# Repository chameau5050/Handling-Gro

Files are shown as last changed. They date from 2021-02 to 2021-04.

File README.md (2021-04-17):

<div id="Handling GRO!">
    <h1>Handling GRO</h1>
    <h3>Projet S4 Université de Sherbrooke</h3>
    <h3>UdeS-GRO | 65<sup>th</sup> Promotion | 2021</h3>
</div>

[//]: # (------------------------------------------------)

<div id="badges">

 

</div>

[//]: # (------------------------------------------------)

**This is an academic project by robotics engineering students at Université de Sherbrooke.**
**Handling GRO is a four degrees of freedom robot.**

<div id="platform" align="center">
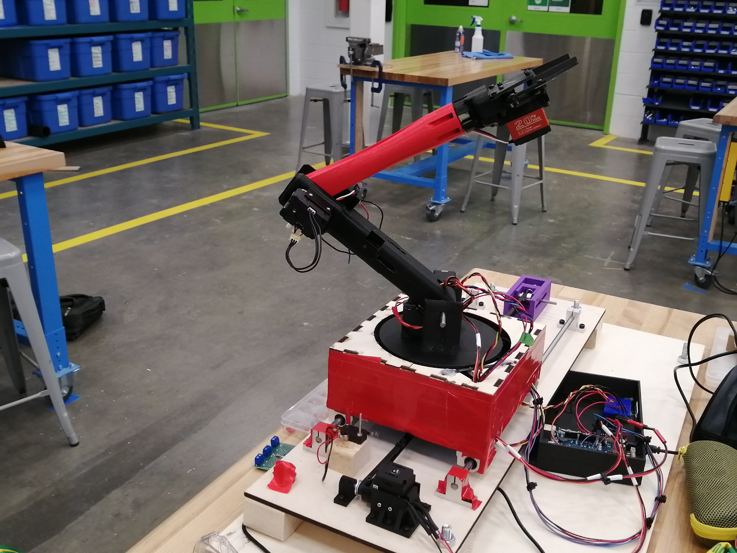
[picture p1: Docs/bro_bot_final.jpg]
Robot Assembly
    
</div>

## Table of Contents
- [Authors](#Authors)
- [Setup](#Setup)
- [Documentation](#Documentation)
- [Recommended manufacturing device](#Recommended_device)
- [External Resources](#Resources)
    - [Single-Board Computer](#Computer)
    - [Controller_OpenCr](#Controller)
    - [Dynamixel motors](#dynamixel) 
    - [Steppermotor](#StepperMotor)
    - [DriveBoard (with steppermotor)](#DriveBoard)
    - [Servomotor](#ServoMotor)
    - [Power Supply: Motor/(OpenCr or Arduino)](#Power)
    - [Linear Rods](#Rods)
    - [Linear bearing](#linear_bearing)
    - [Timing belt](#Timing_belt)
- [License](#License)

[//]: # (------------------------------------------------)
## Authors
- Olivier Demers - _Initial work_ - [chameau5050](https://github.com/chameau5050)
- Jérémy Giguère - _Initial work_ - [gigj1302](https://github.com/gigj1302)
- Philippe Gadeyne - _Initial work_ - [gadp1401](https://github.com/gigj1302)
- Francis Amyot - _Initial work_ - [FrancisAmyot](https://github.com/FrancisAmyot)
- Vincent-Xavier Voyer - _Initial work_ - [Theparky105](https://github.com/Theparky105)

## Setup

1. Buy the component in the [External Resources](#Resources) section.
2. Use the [CAD models](https://github.com/chameau5050/Handling-Gro/tree/main/Mechanical/STL%20(For%203D%20printing)) to 3D print all the different parts of the robot.
3. Assemble the robot according to the [assembly guide](https://github.com/chameau5050/Handling-Gro/blob/main/Docs/Doc_mecanical/Assembly%20manual.pdf).
4. Do the electrical connections using the [electrical schematics](https://github.com/chameau5050/Handling-Gro/blob/main/Electrical_hardware/electrical_wiring_V1.pdf) in the documentation section.
4. Set up the [Raspberry Pi](#Computer) by connecting it with the [OpenCr](#Controller_OpenCr), your computer and the to a power source.
5. Download or clone the repository in the Raspberry Pi.
6. Verify your Python version (3.5 and above) and the port series.
7. Build and transfer all the code to the OpenCr (or Arduino). See [Compilation procedure](https://github.com/chameau5050/Handling-Gro/wiki/setup-IDE-for-ControlMotor(OpenCr)) documentation.
8. Build and transfer all the code to Raspberry Pi. See [Compilation procedure](https://github.com/chameau5050/Handling-Gro/wiki/setup-IDE-for-Application) documentation.
8. Open the interface and look your new Handgling GRO robot in action.
8. Congigure UI with Qt
9. For more information, see the [documentation](https://github.com/chameau5050/Handling-Gro/wiki) section
## Documentation

All the different information is available [here](https://github.com/chameau5050/Handling-Gro/wiki) in the project wiki.

## Recommended manufacturing device
The following rapid design devices are required for this project are:
- For plastic part 
  - 3D Printer
  
- For wood part (choose one of the 2 following choices) 
  - Laser cutter
  - Basic tools for wood (drill, saw, sand paper, ...)

## External Resources
This section specifies the external resources used in the project.

#### Single-Board Computer
- Brand: [Raspberry Pi](https://www.raspberrypi.org/products/raspberry-pi-3-model-b-plus/)
- Model: Raspberry Pi 3 Model 3B+
- Quantity: 1

#### Microcontroller
- Brand: [OpenCr](https://store.arduino.cc/mega-2560-r3)
- Model: OpenCr
- Quantity: 1

#### Microcontroller (optional)
- Brand: [Arduino](https://store.arduino.cc/mega-2560-r3)
- Model: Mega 2560 REV3
- Quantity: 1
- **If you want to use other motors than dynamixel motors, you can.

#### Dynamixel_motors
- Brand: [Dynamixel](https://www.robotis.us/dynamixel-xm430-w350-r/)
- Model: XM430-W350
- Quantity: 4

#### Steppermotor
- Brand: [Elegoo](https://www.elegoo.com/products/elegoo-uln2003-5v-stepper-motor-uln2003-driver-board)
- Model: 28BYJ-48 
- Quantity: 1

#### DriveBoard (with steppermotor)
- Brand: [Elegoo](https://www.elegoo.com/products/elegoo-uln2003-5v-stepper-motor-uln2003-driver-board)
- Model: ULN2003 
- Quantity: 1

#### Servomotor
- Brand: [Miuzei](https://www.amazon.ca/-/fr/Miuzei-num%C3%A9rique-%C3%A9tanche-voiture-contr%C3%B4le/dp/B07MDM1C3M)
- Model: Miuzei Servo Motor 20 Kg
- Quantity: 1

#### Power Supply: Motor/(OpenCr or Arduino)
- Brand: [PowerPayless Inc](https://www.amazon.com/7-5A-Power-Adapter-Device-Payless/dp/B01CYZWAWY)
- Model: B01CYZWAWY (65107)
- Quantity: 1

####  Linear Rods
- Brand: [yqltd](https://www.amazon.ca/CNBTR-Horizontal-Bearing-Bushing-Optical/dp/B01KLE9QEU)
- ASIN: CNBTR4040 road
- Quantity: 2

####  Linear bearing
- Brand: [yqltd](https://www.amazon.ca/CNBTR-Horizontal-Bearing-Bushing-Optical/dp/B01KLE9QEU)
- ASIN: CNBTR4040 bearing
- Quantity: 4

####  Timing belt
- Brand: [Uranny](https://www.amazon.ca/gp/product/B071HKC52V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)
- ASIN: Timing Belt 6mm Wide & 10X 5MM Pulley for 3D Printer
- Quantity: 1

## License
This project is licenced under a   license.

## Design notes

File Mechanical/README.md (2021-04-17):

# Mechanical

All the parts that need to be 3D printed are in the STL folder, see the BOM in the [wiki](https://github.com/chameau5050/Handling-Gro/wiki) to know the number required and to see the step by step assembly guide.

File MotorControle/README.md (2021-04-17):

# Handling-Gro MotorControle section

This is where we implement all the motor control part

Choose if you want to use OpenCr bord or an other board for the motor control.

click on this [link](https://github.com/chameau5050/Handling-Gro/wiki/Motor-Control:-Choice-of-microcontroller) to help you make your choice

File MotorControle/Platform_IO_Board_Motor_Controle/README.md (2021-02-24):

# Handling-Gro

here we implement the All the motor controle part

curently code is running on arduino Mega and can be edit with Visual Studio code with Platform IO extension.

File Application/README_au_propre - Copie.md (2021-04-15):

<div id="Handling GRO">
    <h1>Handling GRO</h1>
    <h3>Projet S4 Université de Sherbrooke</h3>
    <h3>UdeS-GRO | 65<sup>th</sup> Promotion | 2021</h3>
</div>

[//]: # (------------------------------------------------)

<div id="badges">

 

</div>

[//]: # (------------------------------------------------)

**Decrire notre projet en quelques lignes
This is an academic project by robotics engineering undergraduates at Université de Sherbrooke.**
**Handling GRO is a five degrees of freedom fanuc robot. This is an academic project by robotics engineering undergraduates at l'Université de Sherbrooke.**

<div id="platform" align="center">
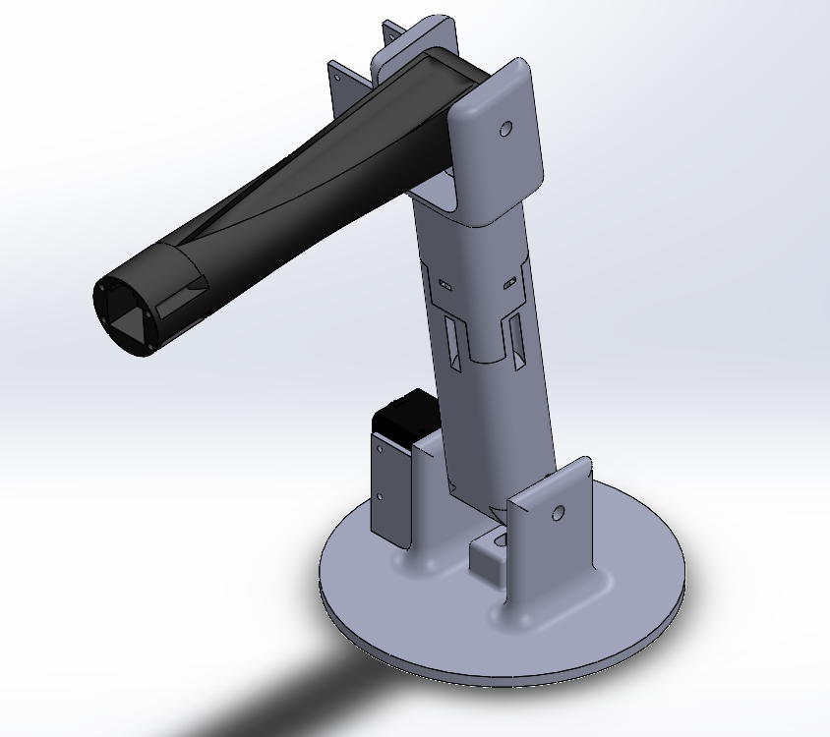
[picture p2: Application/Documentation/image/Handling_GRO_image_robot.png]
Robot Assembly
    
</div>

## Table of Contents
- [Setup](#Setup)
- [Documentation](#Documentation)
- [Platform Operation](#Operation)
- [External Resources](#Resources)
    - [Single-Board Computer](#Computer)
    - [Microcontroller](#Controller)
    - [Servomotors](#Servo)
    - [Power Supply: Motor/Arduino](#Power)
    - [Servo Rods](#Rods)

[//]: # (------------------------------------------------)

## Setup
1. Buy the component in the [External Resources](#Resources) section.
2. Use the [CAD models](https://github.com/SPUdeS/SPUdeS/tree/main/CADs) to 3D print the [base](https://github.com/SPUdeS/SPUdeS/blob/main/CADs/Base.SLDPRT), the [platform](https://github.com/SPUdeS/SPUdeS/blob/main/CADs/Platform.SLDPRT) and the [servo arms](https://github.com/SPUdeS/SPUdeS/blob/main/CADs/Legs.SLDASM).
3. Do the electrical connections using the [electrical schematics](https://github.com/SPUdeS/SPUdeS/blob/main/Documentation/Electical%20schematics.pdf) in the documentation section.
3. Set up the [Raspberry Pi](#Computer) by connecting it with the [Arduino](#Controller), your computer and the to a power source.
4. Download or clone the repository in the Raspberry Pi.
5. Verify your Python version (3.5 and above) and the port series.
6. Build and transfer all the code to the Arduino and Raspberry Pi.
7. Open the interface and look at the [platform operation](#Operation) section.
## Documentation

The dynamic system can be found in the [Geometric model](https://github.com/SPUdeS/SPUdeS/tree/main/Geometric%20model) folder.
## Platform Operation

The camera feed can show the Stewart platform instantly. The platform can be controlled using the following buttons on the interface:

<div id="Interface">
    Platform Assembly
</div>

- It is possible to enter the angle value of all the motor (by default, all the motor should have the same angle).

- The Homing Button brings the stewart platform at its initial centered position.  

- The Move Up Button brings the stewart platform a bit over its actual position
## External Resources
This section specifies the external resources used in the project.

#### Single-Board Computer
- Brand: [Raspberry Pi](https://www.raspberrypi.org/products/raspberry-pi-3-model-b-plus/)
- Model: Raspberry Pi 3 Model 3B+
- Quantity: 1

#### Microcontroller
- Brand: [Arduino](https://store.arduino.cc/mega-2560-r3)
- Model: Mega 2560 REV3
- Quantity: 1

<!--#### Servomotors
- Brand: [Hitec RCD](https://hitecrcd.com/products/servos/sport-servos/analog-sport-servos/hs-422/product)
- Model: HS-422
- Quantity: 6
-->
#### Dynamixel_motors
- Brand: [Dynamixel](https://www.robotis.us/dynamixel-xm430-w350-r/)
- Model: XM430-W350
- Quantity: 4

#### SteperMotors
- Brand: [Elegoo](https://www.elegoo.com/products/elegoo-uln2003-5v-stepper-motor-uln2003-driver-board)
- Model: 28BYJ-48 
- Quantity: 1

#### DriveBoard
- Brand: [Elegoo](https://www.elegoo.com/products/elegoo-uln2003-5v-stepper-motor-uln2003-driver-board)
- Model: ULN2003 
- Quantity: 1
<!--
#### Servomotors
- Brand: [Adafruit](https://www.amazon.ca/Adafruit-2201-Sub-micro-Servo-SG51R/dp/B0137LG0KW)
- Model: SG51R
- Quantity: 6

#### Power Supply: Motor/Arduino
- Brand: [CUI Inc.](https://www.digikey.com/en/products/detail/cui-inc/SWI10-5-N-P5/6618696)
- Model: SWI10-5-N
- Quantity: 1
-->
####  Linear Rods
- Brand: [yqltd](https://www.amazon.ca/CNBTR-Horizontal-Bearing-Bushing-Optical/dp/B01KLE9QEU)
- ASIN: CNBTR4040 road
- Quantity: 2

####  Linear bearing
- Brand: [yqltd](https://www.amazon.ca/CNBTR-Horizontal-Bearing-Bushing-Optical/dp/B01KLE9QEU)
- ASIN: CNBTR4040 bearing
- Quantity: 4

## License
This project is licenced under a   license.

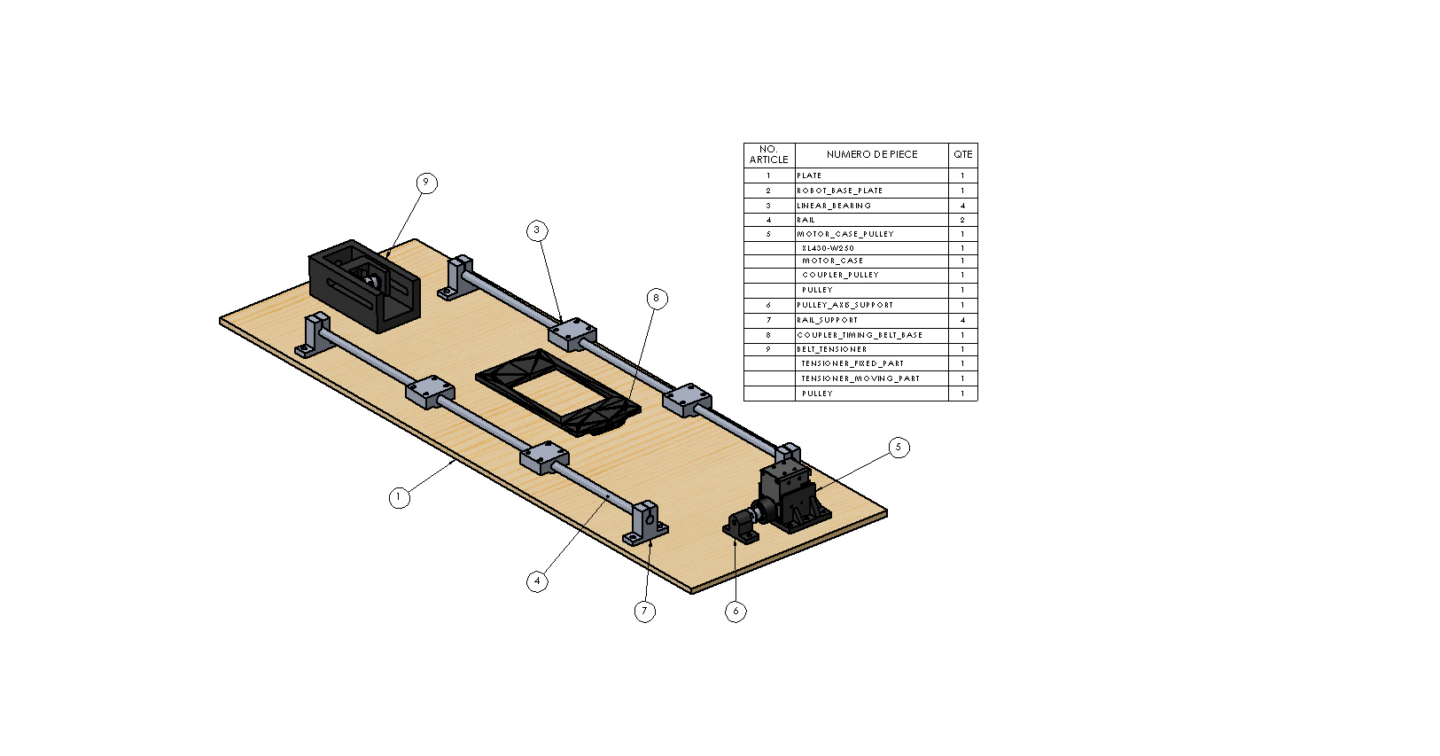
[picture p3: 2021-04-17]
Mechanical/linear_axis/linear_axis_plan.JPG

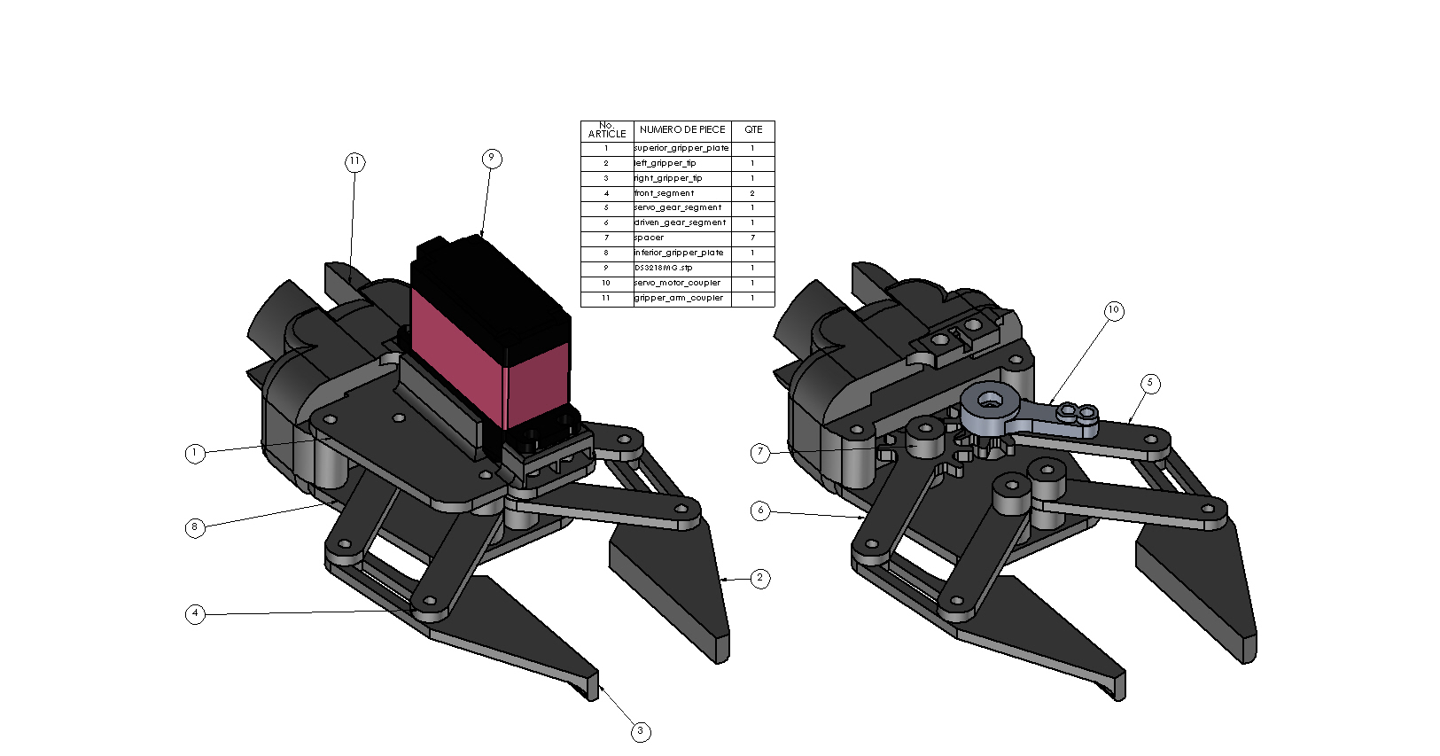
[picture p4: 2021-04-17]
Mechanical/Gripper_servo_motor/gripper_plan.JPG

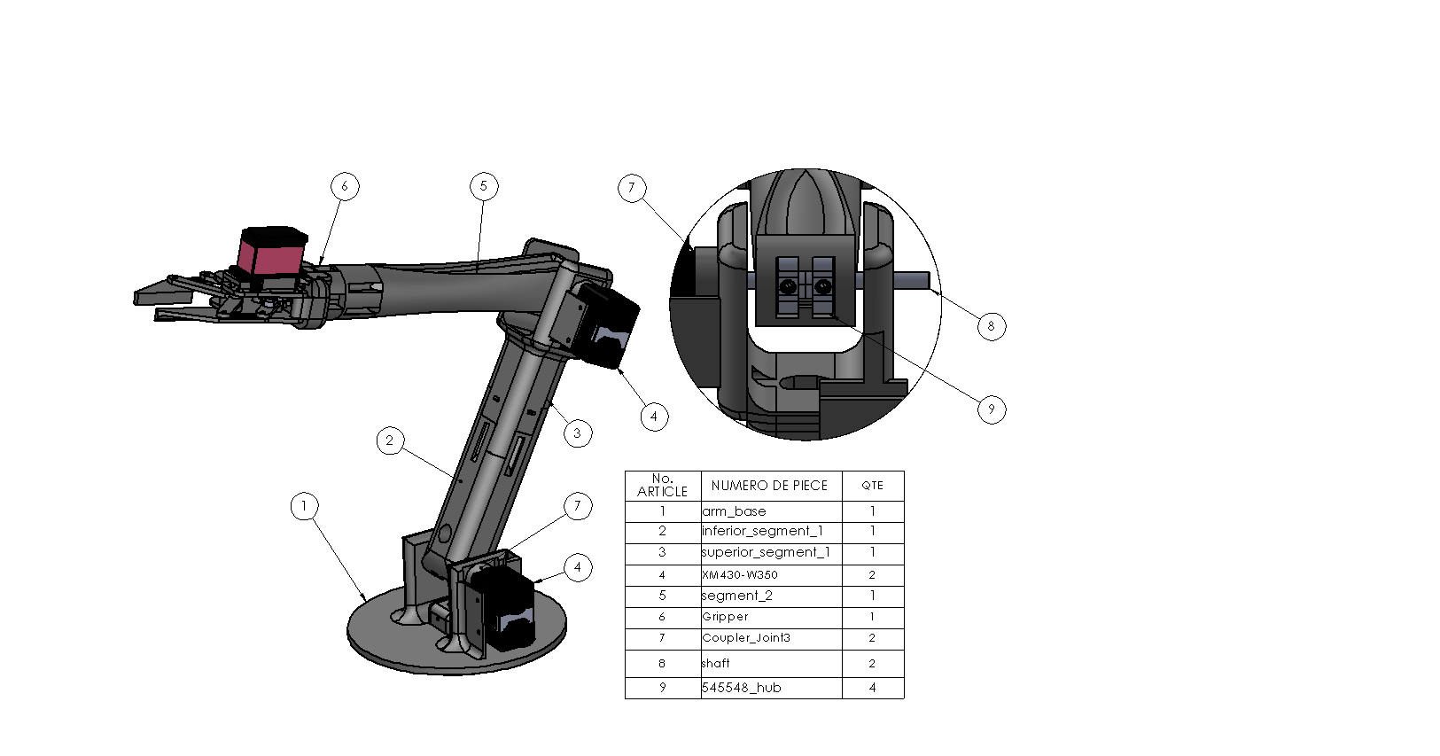
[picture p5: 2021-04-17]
Mechanical/Arm2.0/arm_plan.JPG

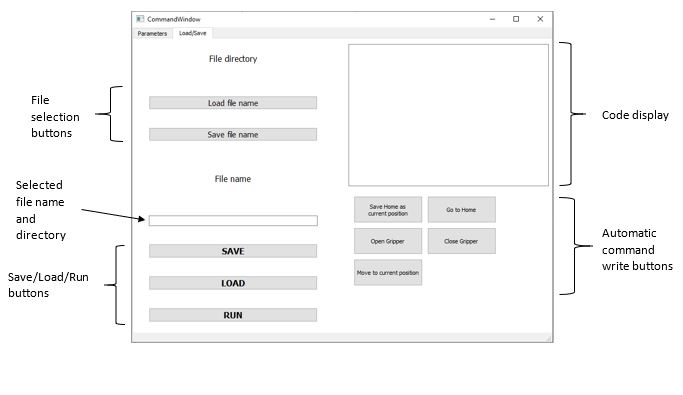
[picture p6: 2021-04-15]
Docs/Doc_picture_UI/Picture_UI_P2.JPG

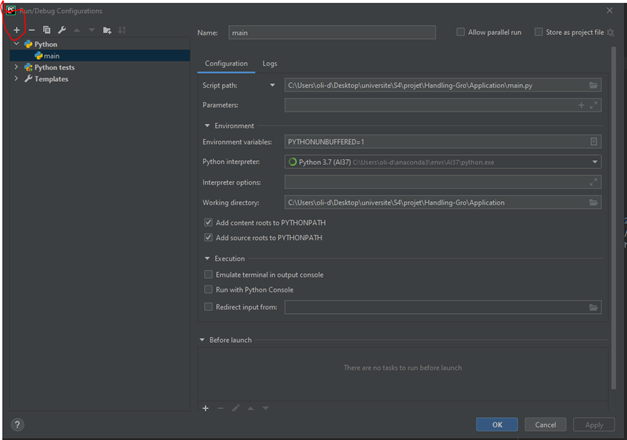
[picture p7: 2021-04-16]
Docs/Doc_picture_Application/addExecutionConfig.png

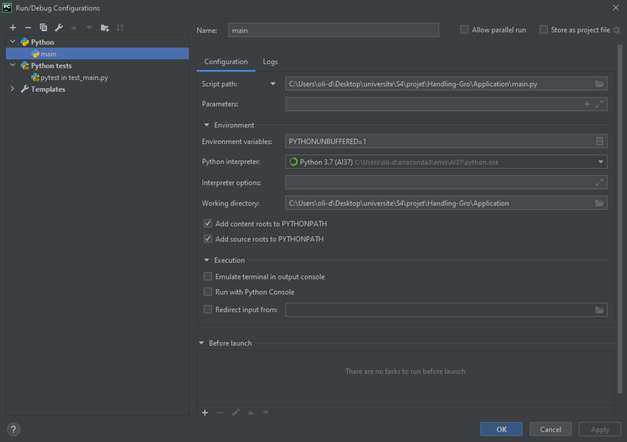
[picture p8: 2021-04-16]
Docs/Doc_picture_Application/selectMain.png

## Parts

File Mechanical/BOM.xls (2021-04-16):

No. ARTICLE | NUMERO DE PIECE | DESCRIPTION | QTE
1 | plate | 300x700x6,35 mm laser cuted plywood | 1
2 | XL430-W250 | Dynamixel motor | 2
3 | rail | 8 mm Dia. 50 mm long aluminium cylinder | 2
4 | motor_case | 3D printed | 1
5 | coupler_pulley | 3D printed | 1
6 | pulley | 11 mm Dia. Timing belt pulley | 2
7 | 91292A832 | M2-8mm_91292A832_TYPE 18-8 SS SOCKET HEAD CAP SCREW | 6
8 | pulley_axis_support | 3D printed | 1
9 | rail_support | Rail hub | 4
10 | coupler_timing_belt_b ase | 3D printed | 1
11 | tensioner_fixed_part | 3D printed | 1
12 | tensioner_moving_part | 3D printed | 1
13 | pulley_long_shaft | 5mm Dia. 60 mm long metal cylinder | 1
14 | M10-75mm screw | M10-75mm_TYPE 18-8 SS HEX HEAD CAP SCREW | 1
15 | M10-NUT | M10-NUT_TYPE 18-8 SS THIN HEX NUT - DIN 439B | 1
16 | linear_bearing | Linear ball bearing | 4
17 | 91292A115 | M3-16mm_91292A115_TYPE 18-8 SS SOCKET HEAD CAP SCREW | 11
18 | 90710A030 | M3-NUT_90710A030_TYPE 18-8 SS THIN HEX NUT - DIN 439B | 28
19 | 91292A118 | M4-20mm_91292A118_TYPE 18-8 SS SOCKET HEAD CAP SCREW | 12
20 | 91292A118 | M5-20mm_TYPE 18-8 SS SOCKET HEAD CAP SCREW | 2
21 | 90710A035 | M4-NUT_90710A035_TYPE 18-8 SS THIN HEX NUT - DIN 439B | 24
22 | 90710A035 | M5-NUT_TYPE 18-8 SS THIN HEX NUT - DIN 439B | 2
23 | pulley_shaft | 5mm Dia. 40 mm long metal cylinder | 1
24 | 91292A108 | M4-8mm_91292A108_TYPE 18-8 SS SOCKET HEAD CAP SCREW | 1
25 | timing_belt | 1,6 m long min. 5 mm large (link 2) | 1
26 | robot_base_plate | 3D printed | 1
27 | Support_Bearing_V4 | 3D printed | 1
28 | Coupler_Joint1 | 3D printed | 1
29 | bearing | Rubber seal ball bearing 9,52 mm Int. Dia. 22,22 mm Ext. Dia. | 3
30 | 535198 | Bearing 6,35 mm Int. Dia. 12,7 mm Ext. Dia. | 1
31 | 6432K12 | Plain bearing | 1
32 | shaft | 2 inch D shaft | 1
33 | 91292A112 | M3-8mm_91292A112_TYPE 18-8 SS SOCKET HEAD CAP SCREW | 2
34 | 91292A002 | M2-16mm_91292A002_TYPE 18-8 SS SOCKET HEAD CAP SCREW | 4
35 | 91292A118 | M4-16mm_91292A118_TYPE 18-8 SS SOCKET HEAD CAP SCREW | 8
36 | arm_base | 3D printed | 1
37 | inferior_segment_1 | 3D printed | 1
38 | superior_segment_1 | 3D printed | 1
39 | XM430-W350 | Dynamixel motor | 2
40 | segment_2 | 3D printed | 1
41 | superior_gripper_plate | 3D printed | 1
42 | left_gripper_tip | 3D printed | 1
43 | right_gripper_tip | 3D printed | 1
44 | front_segment | 3D printed | 2
45 | servo_gear_segment | 3D printed | 1
46 | driven_gear_segment | 3D printed | 1
47 | spacer | 3D printed | 7
48 | inferior_gripper_plate | 3D printed | 1
49 | DS3218MG.stp | Miuzei DS3218 servo motor | 1
50 | servo_motor_coupler | DS3218 shaft coupler | 1
51 | gripper_arm_coupler | 3D printed | 1
52 | 91292A123 | M3-25mm_TYPE 18-8 SS SOCKET HEAD CAP SCREW | 5
53 | 91292A118 | M4-12mm_TYPE 18-8 SS SOCKET HEAD CAP SCREW | 4
54 | 91292A114 | M3-12mm_91292A114_TYPE 18-8 SS SOCKET HEAD CAP SCREW | 4
55 | coupler_joint3 | 3D printed | 2
56 | shaft | 3 inch D shaft | 2
57 | 545548 | Set screw hub | 4
58 | 91292A123 | M3-20mm_91292A123_TYPE 18-8 SS SOCKET HEAD CAP SCREW | 16
59 | 91292A832 | M2-8mm_91292A832_TYPE 18-8 SS SOCKET HEAD CAP SCREW | 14
60 | box_top | 6,35 mm thick laser cuted plywood | 2
61 | box1 | 6,35 mm thick laser cuted plywood | 2
62 | box2 | 6,35 mm thick laser cuted plywood | 2

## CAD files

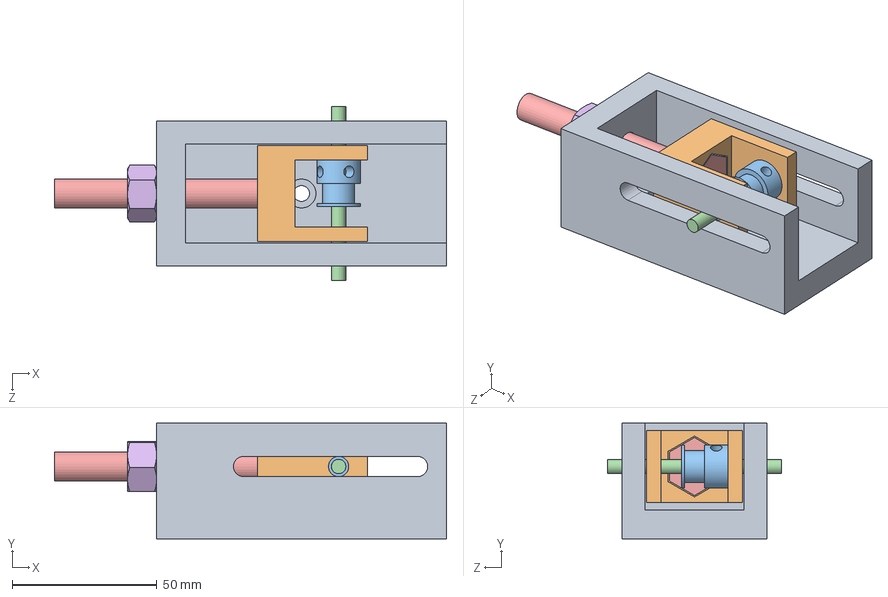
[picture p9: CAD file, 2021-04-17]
Mechanical/linear_axis/belt_tensioner/belt_tensioner.SLDASM
135.2 x 40.0 x 60.0 mm
tensioner_fixed_part
tensioner_moving_part
pulley
pulley_long_shaft
M10-75mm_TYPE 18-8 SS HEX HEAD CAP SCREW
M10-NUT_TYPE 18-8 SS THIN HEX NUT - DIN 439B (1)

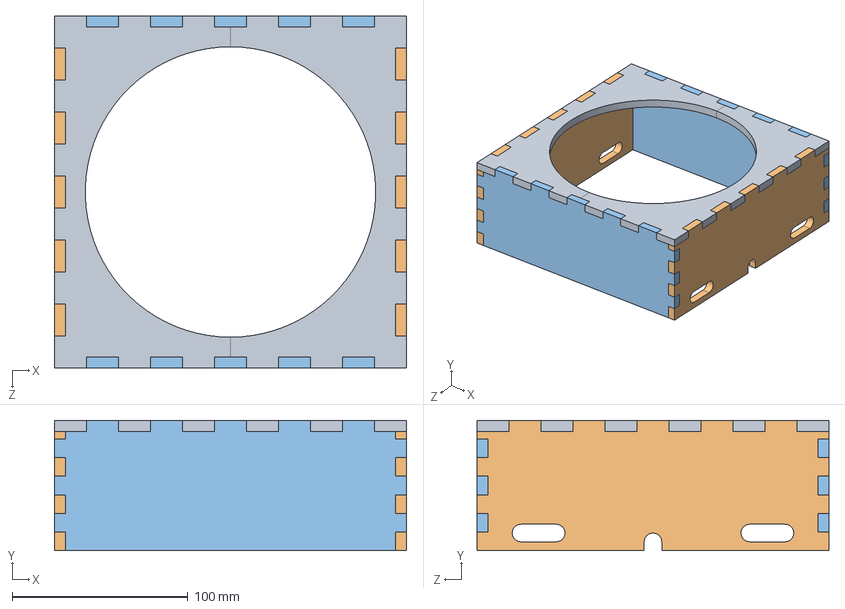
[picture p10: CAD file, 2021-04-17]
Mechanical/Socle/base_box.SLDASM
200.0 x 74.0 x 200.0 mm
box_top x 2

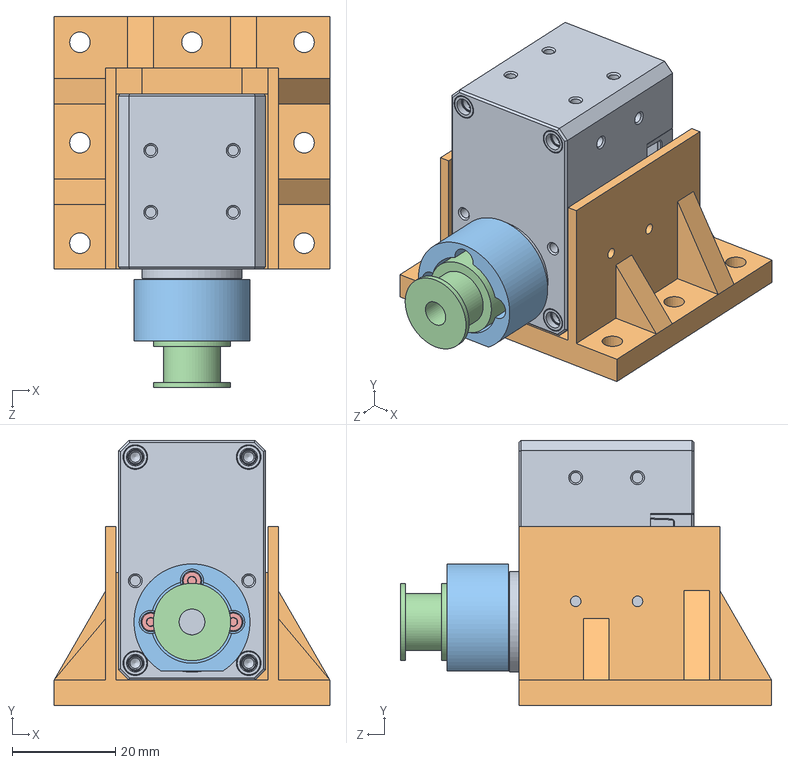
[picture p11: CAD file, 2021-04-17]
Mechanical/linear_axis/motor_case_pulley.SLDASM
53.5 x 51.5 x 72.0 mm
XL430-W250
motor_case
coupler_pulley
pulley
M2-4mm_TYPE 18-8 SS SOCKET HEAD CAP SCREW x 3

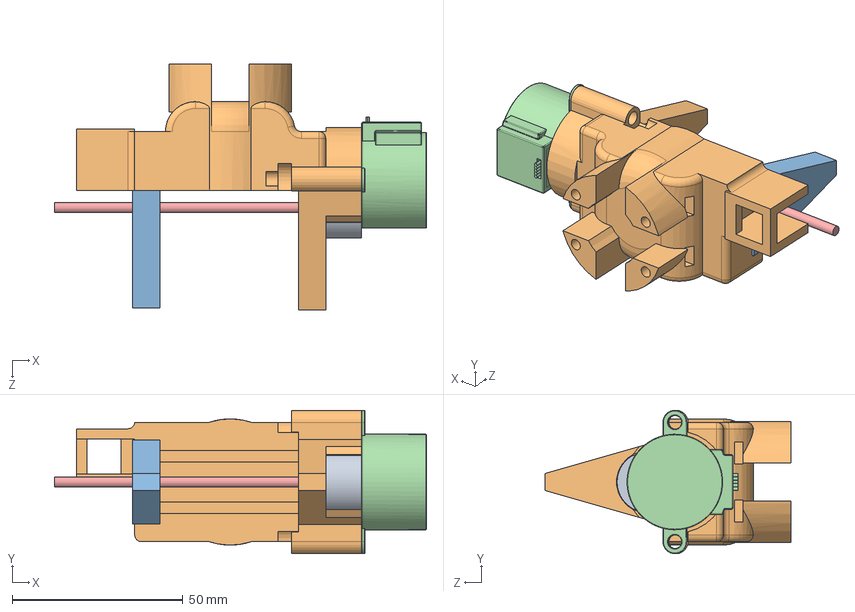
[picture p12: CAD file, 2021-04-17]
Mechanical/Gripper_threaded_shaft/Gripper.SLDASM
109.0 x 42.0 x 72.0 mm
coupler_shaft_motor
stationary_gripper_part
moving_gripper_part
stepper_28BYJ-48.stp
80mm_threaded_shaft

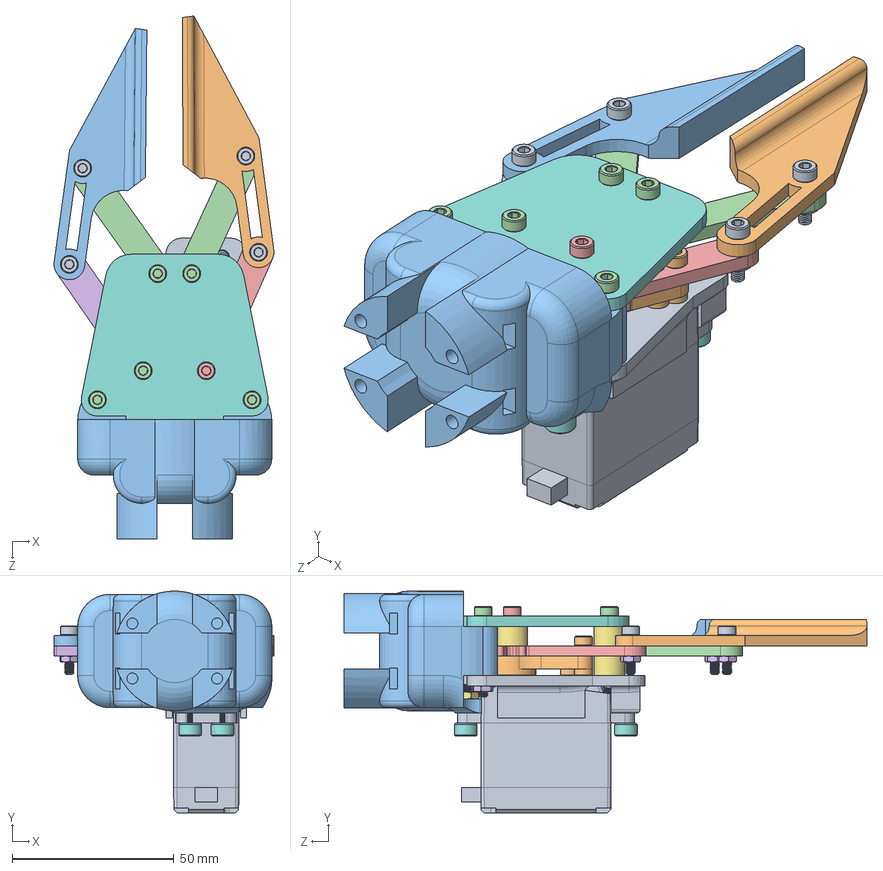
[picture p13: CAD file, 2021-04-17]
Mechanical/Gripper_servo_motor/gripper.SLDASM
67.9 x 68.5 x 161.6 mm
superior_gripper_plate
left_gripper_tip
right_gripper_tip
front_segment x 2
servo_gear_segment
driven_gear_segment
spacer x 7
inferior_gripper_plate
DS3218MG.stp
servo_motor_coupler
gripper_arm_coupler
M3-25mm_TYPE 18-8 SS SOCKET HEAD CAP SCREW x 5
M3-16mm_91292A115_TYPE 18-8 SS SOCKET HEAD CAP SCREW
M3-NUT_90710A030_TYPE 18-8 SS THIN HEX NUT - DIN 439B x 9
M4-NUT_90710A035_TYPE 18-8 SS THIN HEX NUT - DIN 439B x 4
M4-12mm_TYPE 18-8 SS SOCKET HEAD CAP SCREW x 4
M3-12mm_91292A114_TYPE 18-8 SS SOCKET HEAD CAP SCREW x 4
M3-8mm_91292A112_TYPE 18-8 SS SOCKET HEAD CAP SCREW

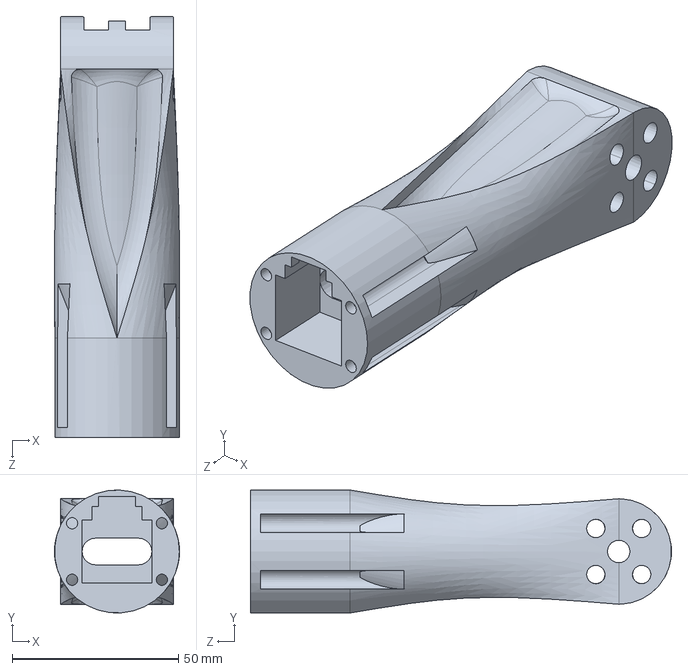
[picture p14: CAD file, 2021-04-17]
Mechanical/Arm2.0/Bras_Horizontal2.SLDPRT
37.7 x 37.0 x 126.7 mm

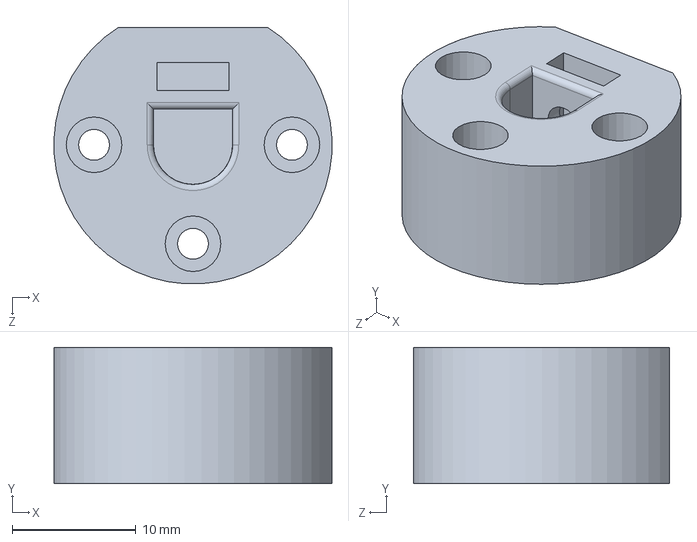
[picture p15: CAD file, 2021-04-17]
Mechanical/Coupler/coupler_joint3.SLDPRT
22.5 x 11.0 x 20.7 mm

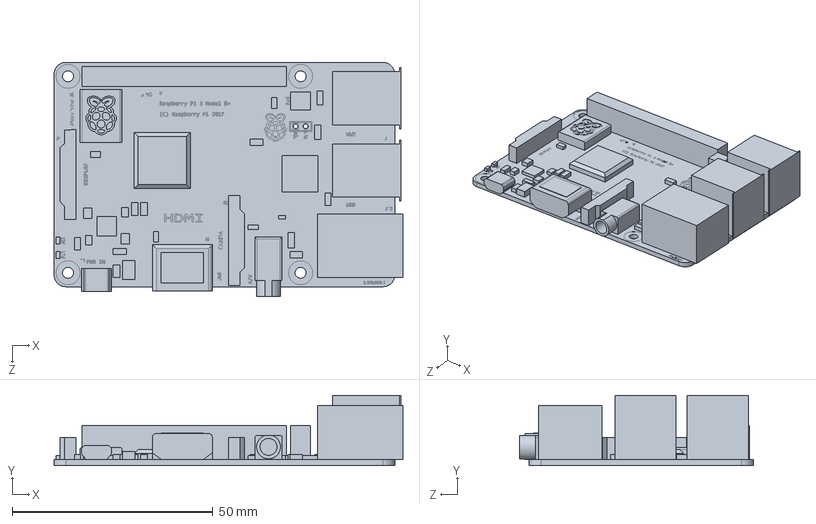
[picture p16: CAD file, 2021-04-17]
Mechanical/Electronique/Rpi3Bplus.SLDPRT
87.0 x 17.5 x 58.5 mm

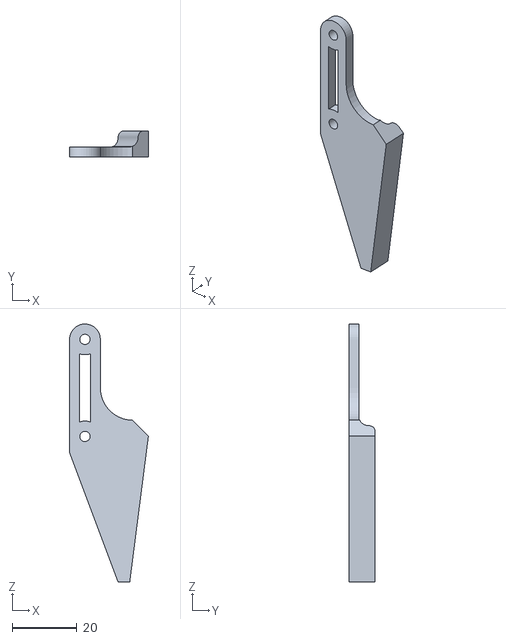
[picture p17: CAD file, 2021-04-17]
Mechanical/Gripper_servo_motor/Gripp.STL
24.4 x 8.17 x 79.7

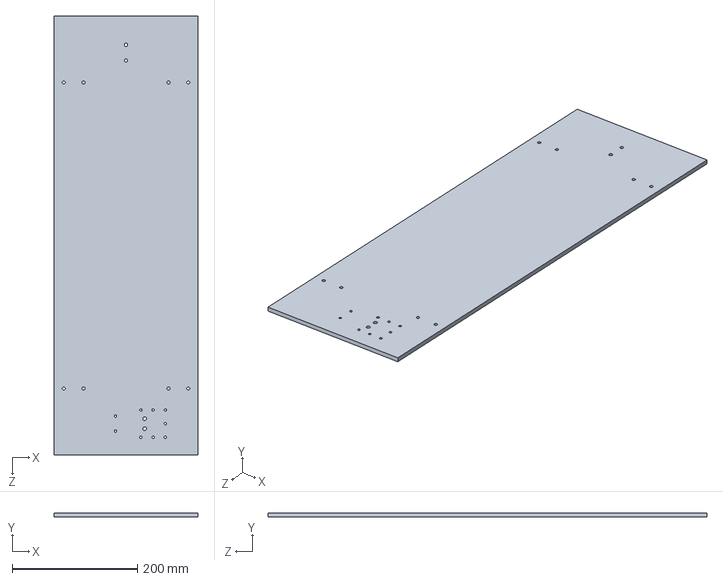
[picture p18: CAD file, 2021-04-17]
Mechanical/linear_axis/plate.SLDPRT
229.5 x 6.35 x 700.0 mm

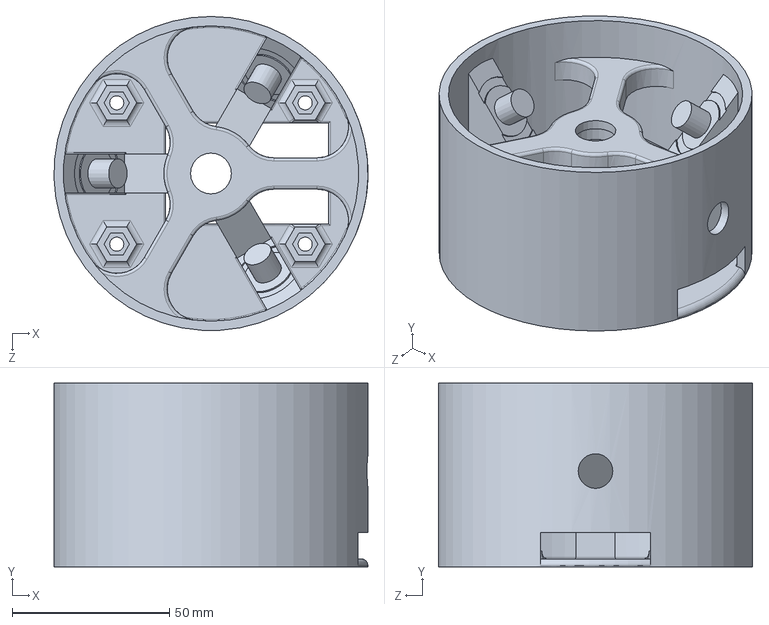
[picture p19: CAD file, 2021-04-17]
Mechanical/Socle/Support_Bearing_V4.SLDPRT
100.0 x 58.5 x 100.0 mm

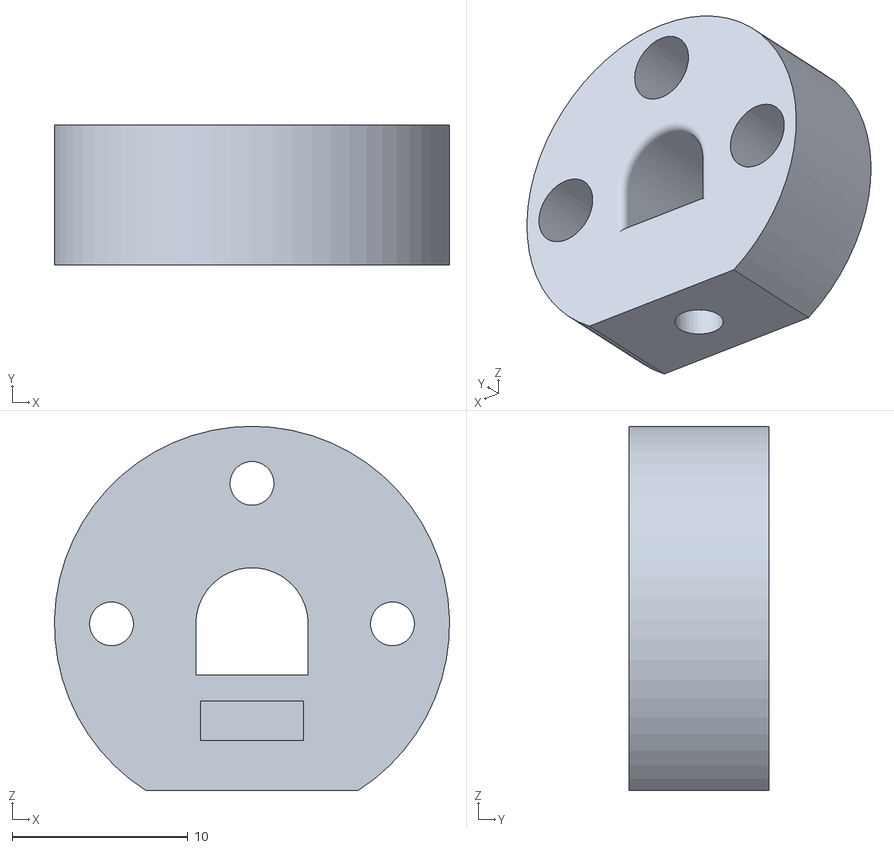
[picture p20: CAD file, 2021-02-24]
Mechanical/STL (For 3D printing)/1X_Coupler_Joint3.STL
22.5 x 8.00 x 20.8

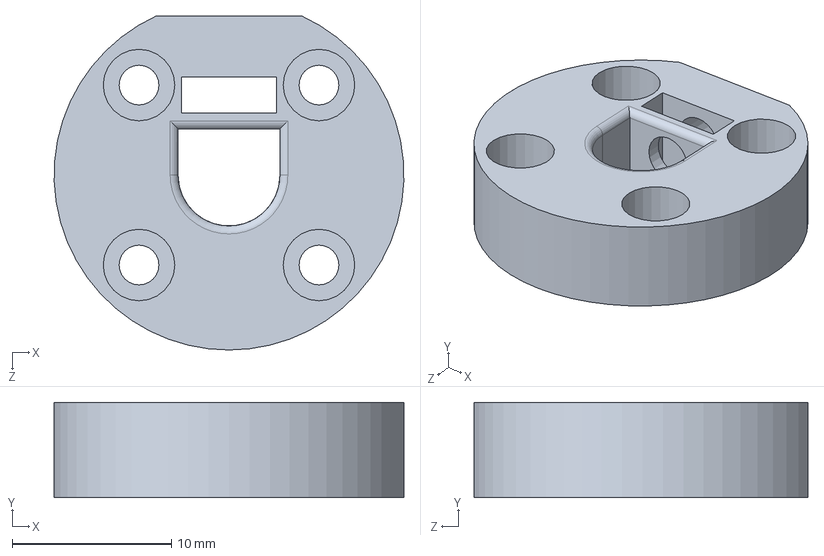
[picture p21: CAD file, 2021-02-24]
Mechanical/Coupler/Coupler_1.SLDPRT
22.0 x 6.00 x 21.0 mm

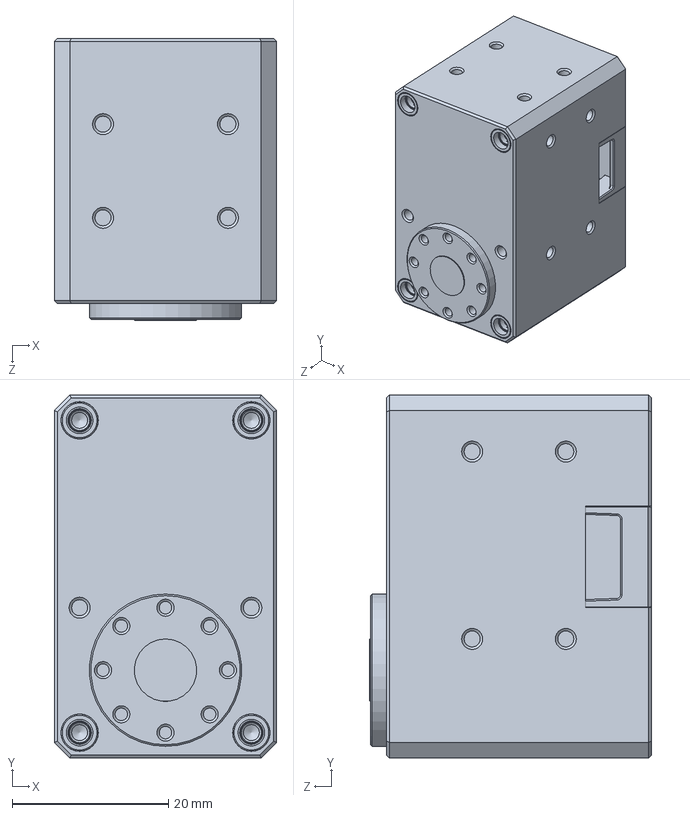
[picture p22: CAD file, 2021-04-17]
Mechanical/Electronique/XL430-W250.SLDPRT
28.5 x 46.5 x 36.2 mm

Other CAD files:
Mechanical/Gripper_threaded_shaft/stepper_28BYJ-48.stp.SLDPRT
Mechanical/Segment_2/Coupler_Joint3.STL
Mechanical/Arm2.0/short_segment_2.SLDPRT
Mechanical/Gripper_servo_motor/Gripp2.STL
Mechanical/Arm2.0/BArm.STL
Mechanical/Arm2.0/Base OpenCR.SLDPRT
Mechanical/Arm2.0/Bras_Horizontal.STL
Mechanical/Arm2.0/VArm1.SLDPRT
Mechanical/Arm2.0/VArm1_bolt.STL
Mechanical/Arm2.0/VArm2_bolt.STL
Mechanical/Arm2.0/arm_base.SLDPRT
Mechanical/Arm2.0/arm_plan.SLDDRW
Mechanical/Arm2.0/inferior_segment_1.SLDPRT
Mechanical/Arm2.0/segment_2.SLDPRT
Mechanical/Arm2.0/short_segment_2.STL
Mechanical/Arm2.0/superior_segment_1.SLDPRT
Mechanical/Coupler/Coupler_2.SLDPRT
Mechanical/Electronique/OpenCR.SLDPRT
Mechanical/Electronique/XM430-W350.SLDPRT
Mechanical/Electronique/x-430_idle.stp
Mechanical/Gripper_servo_motor/Base grip.STL
Mechanical/Gripper_servo_motor/DS3218MG.stp
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

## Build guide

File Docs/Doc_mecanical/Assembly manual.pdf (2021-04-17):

## 1.COUPLER MOTOR

- Insert a nut in one coupler joint 2 and in two coupler joints 3
- Bolt the coupler joint 2 on a W250 Dynamixel motor and bolt each coupler joints

3 on a W350 Dynamixel motor

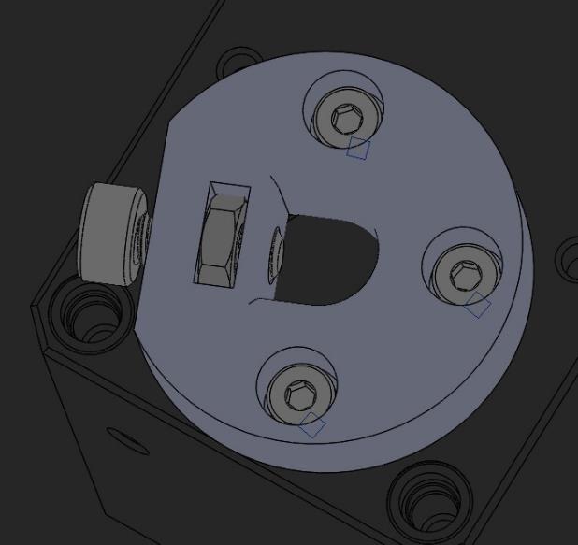
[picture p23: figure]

- Bolt the coupler pulley into a W250 Dynamixel motor
- Insert the shaft in the pulley and tighten it with a bolt through the pulley coupler

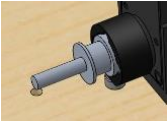
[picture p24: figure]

## 2.LINEAR AXIS

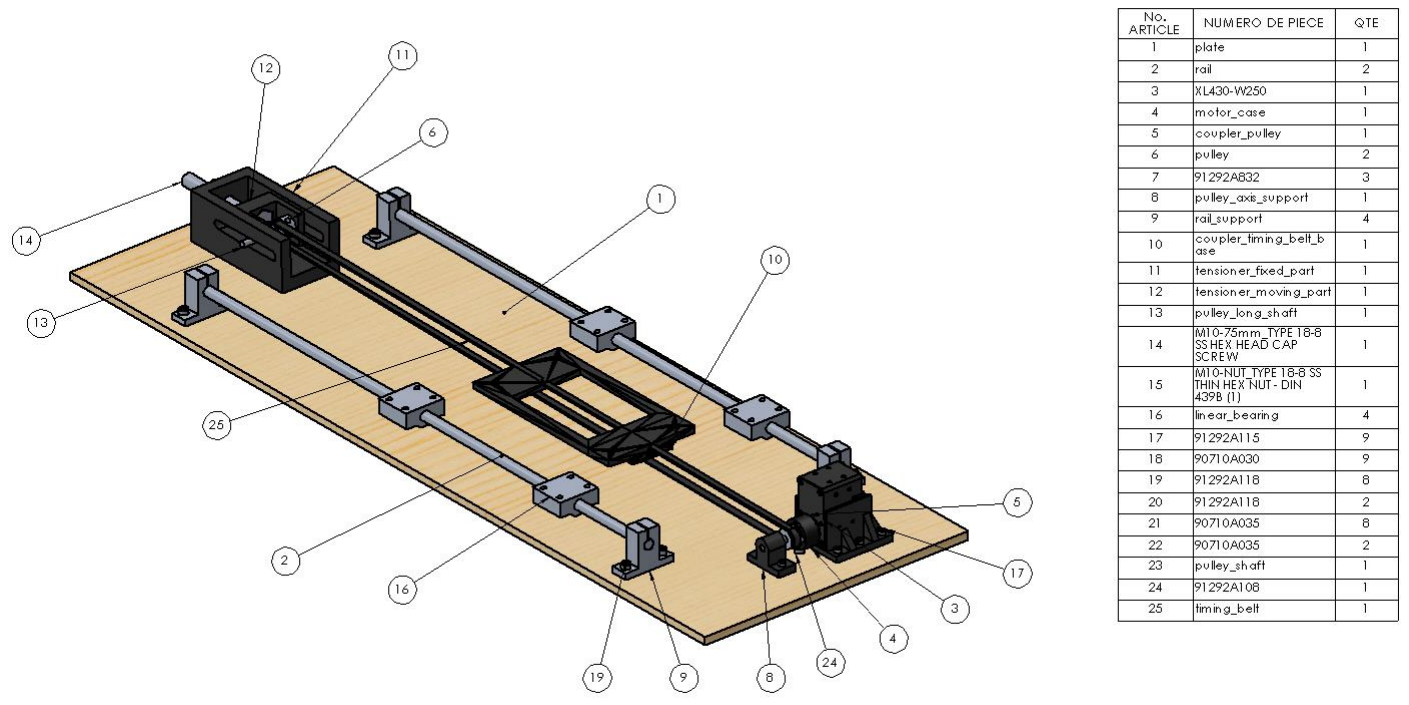
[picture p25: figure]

- Laser cut a 300 mm x 700 mm x 6.35 mm plywood

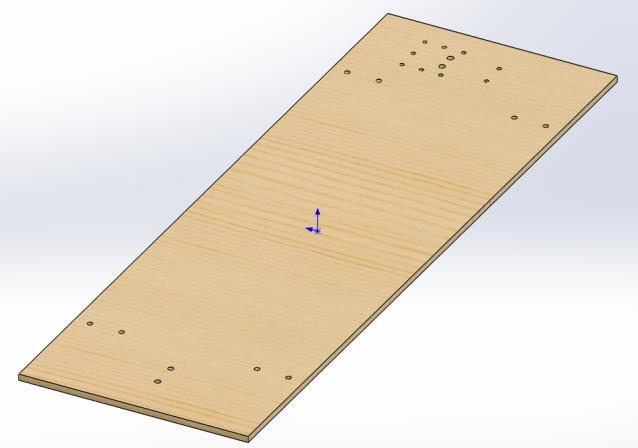
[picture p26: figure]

- Fix each part with bolt and nut

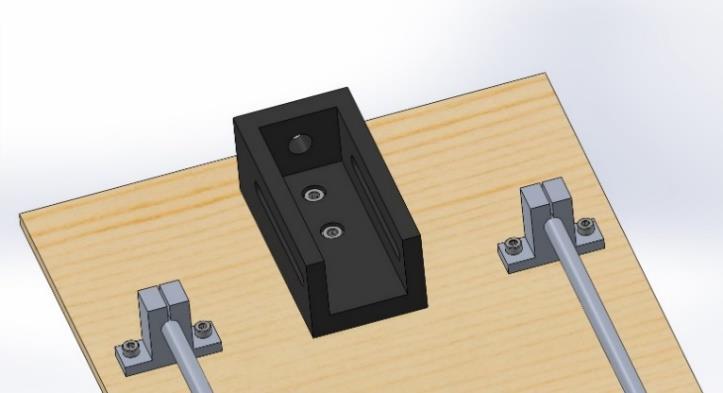
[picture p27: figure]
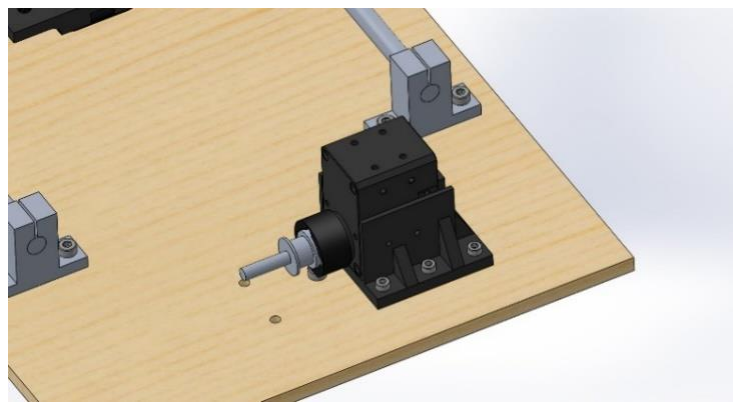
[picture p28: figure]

- Put the timing belt, then the support axis pulley

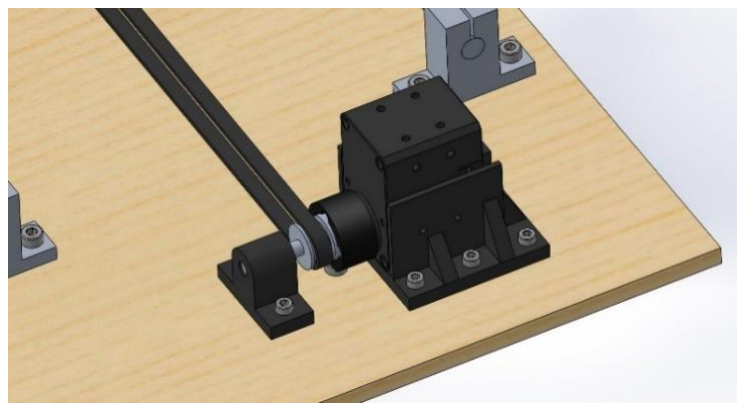
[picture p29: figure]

- Fix the timing belt to the base coupler with tie wraps
- Assembly the belt tensioner
- Pass the timing belt around the belt tensioner pulley and fix it on the timing belt

base coupler

## 3.SOCLE

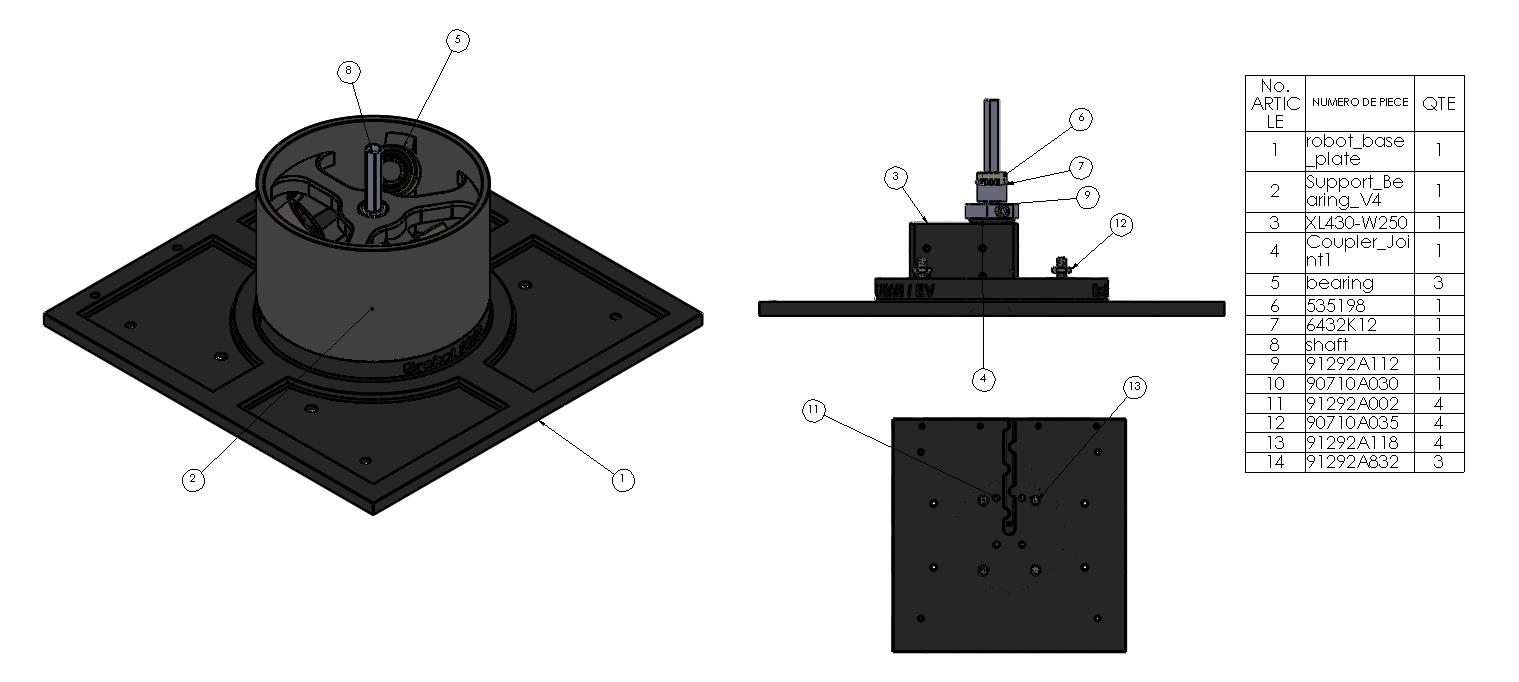
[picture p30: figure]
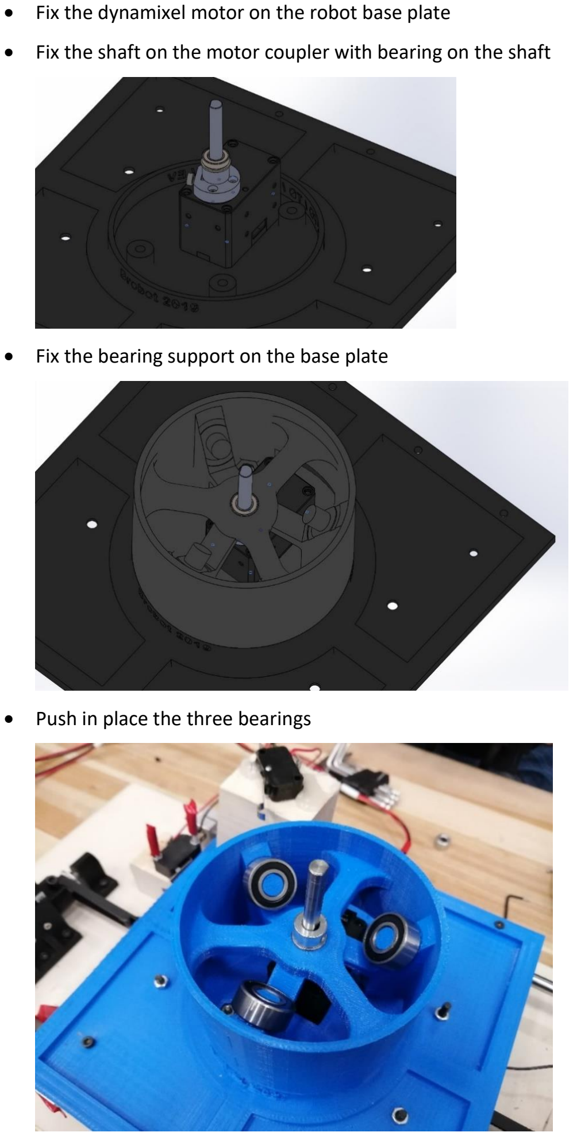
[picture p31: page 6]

- Fix the dynamixel motor on the robot base plate
- Fix the shaft on the motor coupler with bearing on the shaft
- Fix the bearing support on the base plate
- Push in place the three bearings

## 4.ROBOT ARM

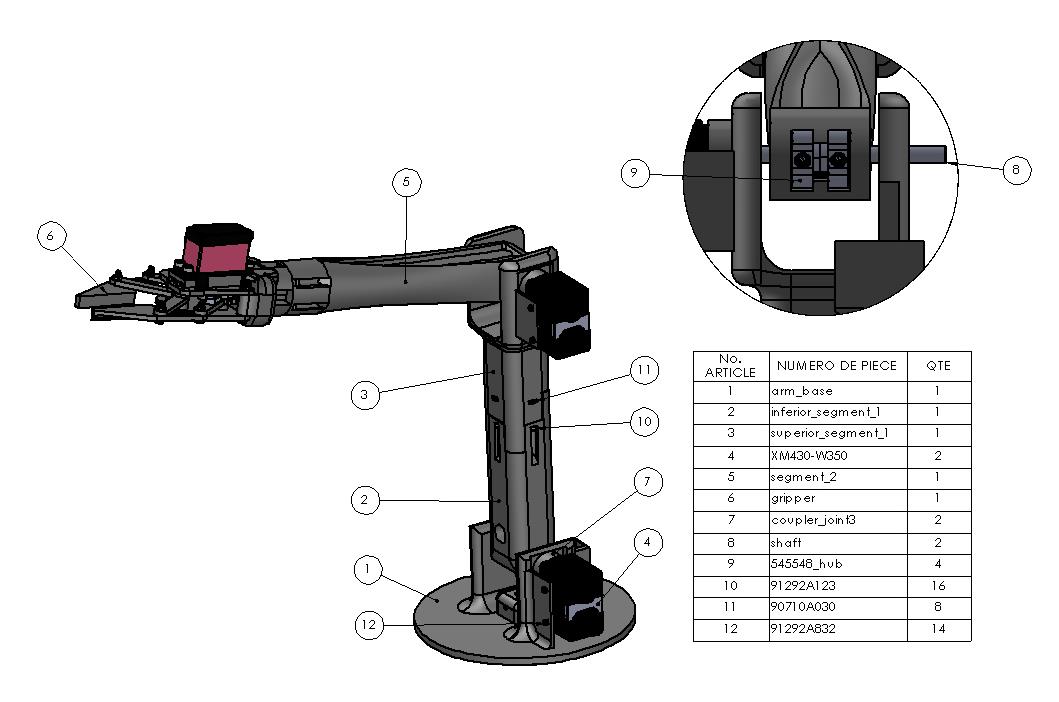
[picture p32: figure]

- Push in place the 2 sets screw hub in inferior segment 1 and in segment 2

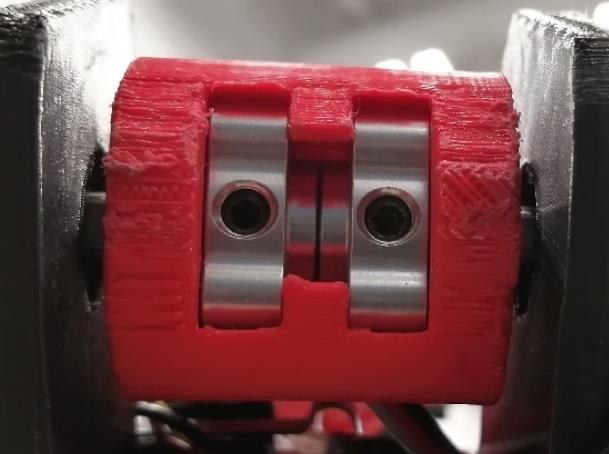
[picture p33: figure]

- Bolt the hub together
- Bolt inferior segment 1 with superior segment 1

- Fix the two shafts in their motor coupler and pass it through the robot

base/superior segment 1 and the set screw hub

- Tighten each screw of the hub onto the flat surface of the shaft
- Fix each motor on both walls

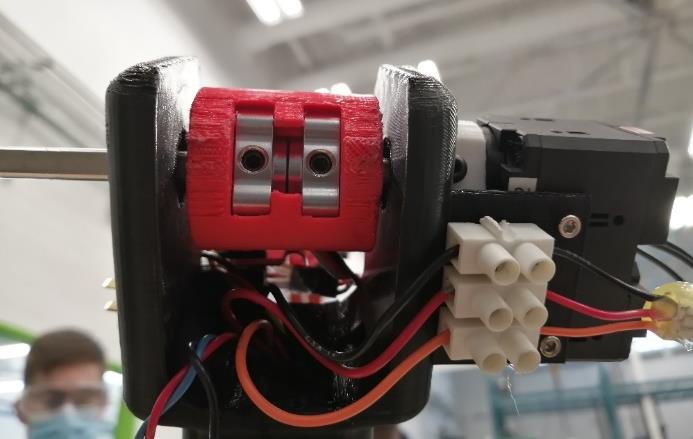
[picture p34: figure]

## 5.GRIPPER

- Put these 4 bolts in the inferior gripper plate

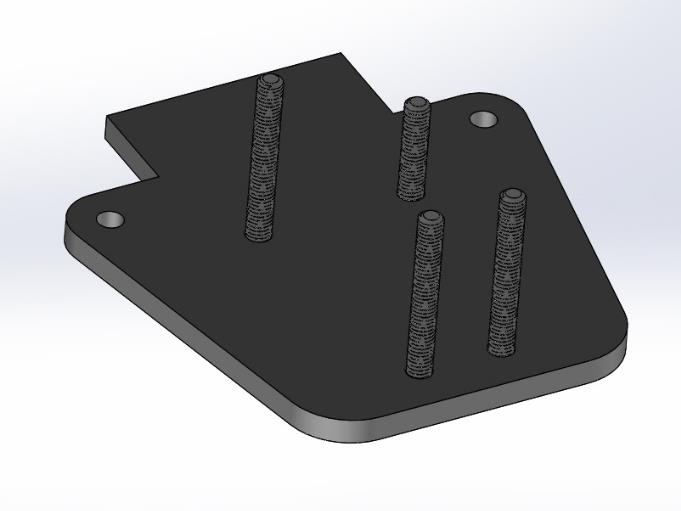
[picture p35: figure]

- Put in place the spacer, the gear segments, and the front segments

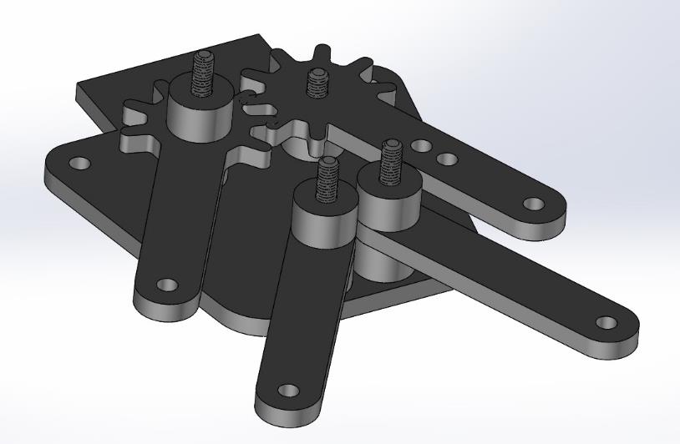
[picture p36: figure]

- Fix the servomotor into the superior gripper plate

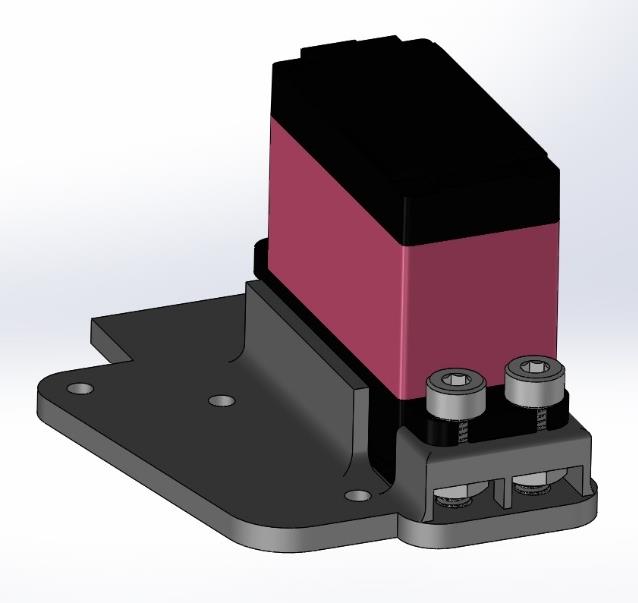
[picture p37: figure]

- Fix the servomotor coupler on the motor shaft

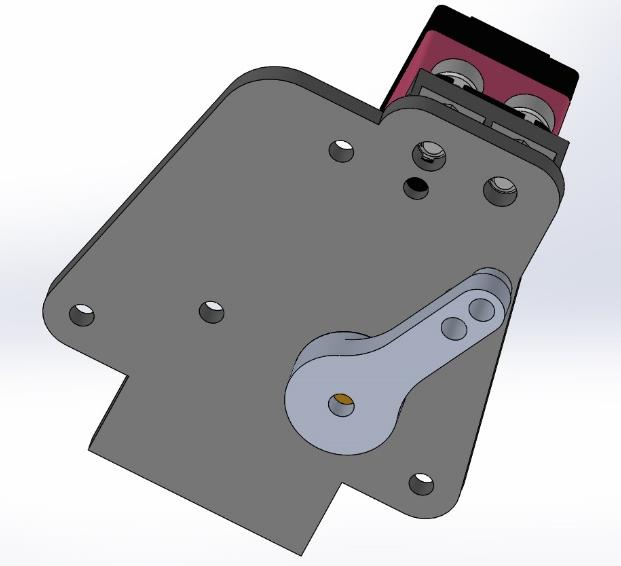
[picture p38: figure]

- Put the superior gripper plate on top and bolt it (not too tight)

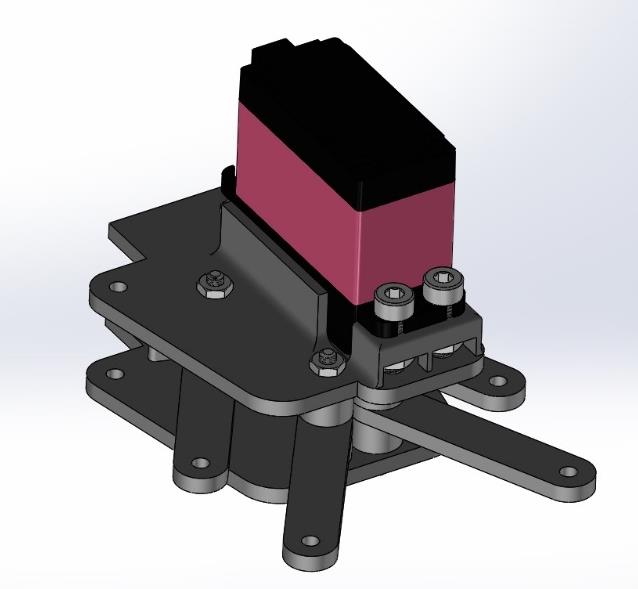
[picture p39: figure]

- Fix the servo gear segment into the servomotor coupler

- Push the two gripper plates into the arm coupler, bolt the plates to the arm

coupler, and bolt the motor with the arm coupler

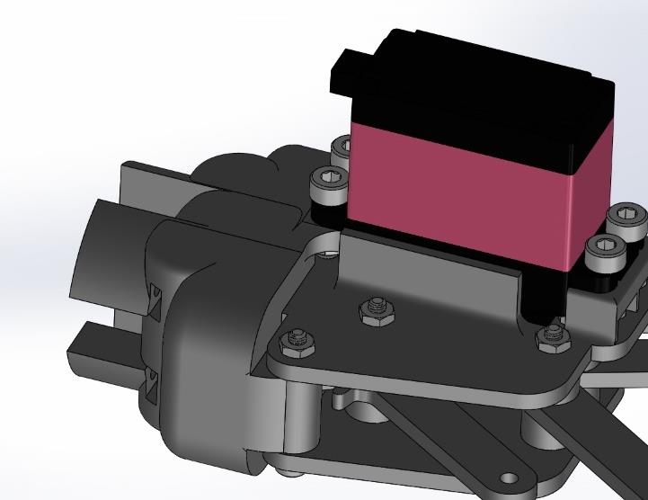
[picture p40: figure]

- Fix the two gripper tips

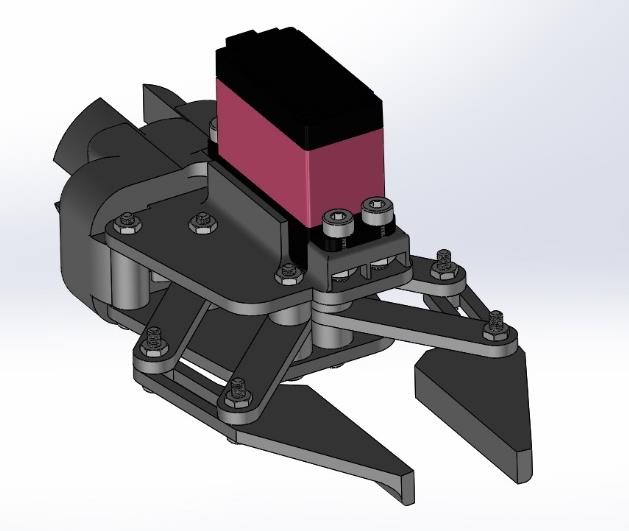
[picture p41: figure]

## 6.FINAL ASSEMBLY

- Place the base robot plate on the linear bearing and bolt the bearing and the

timing belt coupler with the plate

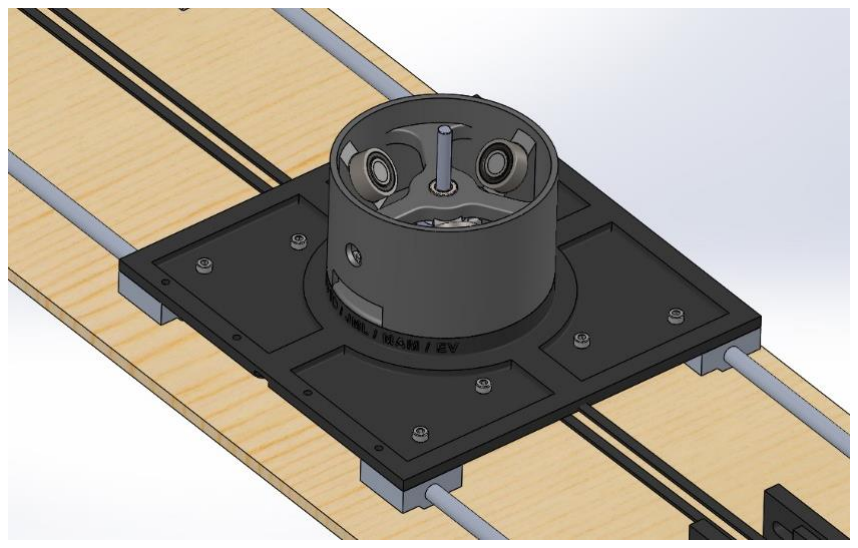
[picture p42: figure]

- Bolt the gripper arm coupler with segment 2

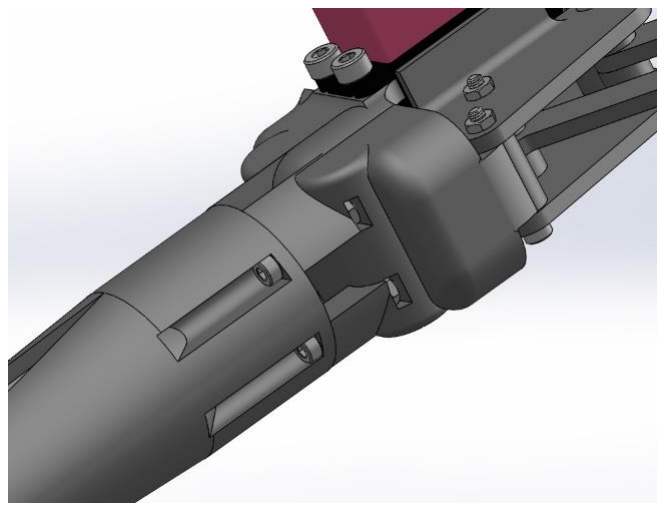
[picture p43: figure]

- Place the arm base on the three bearings

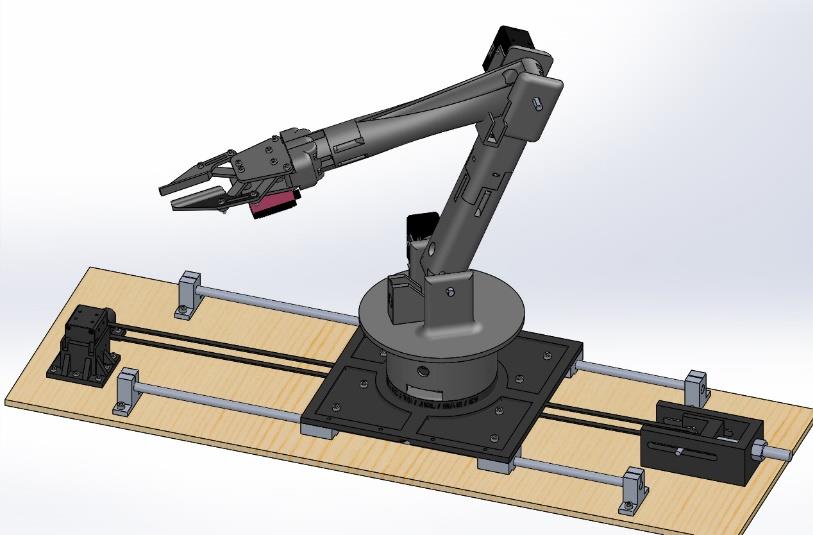
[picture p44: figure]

- Place the box on the robot base plate

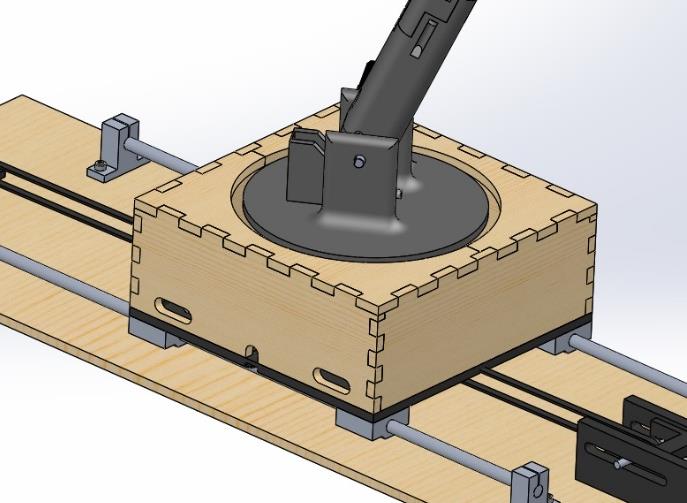
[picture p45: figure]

- Place a nut onto the flat surface of the shaft and tighten the bolt into it

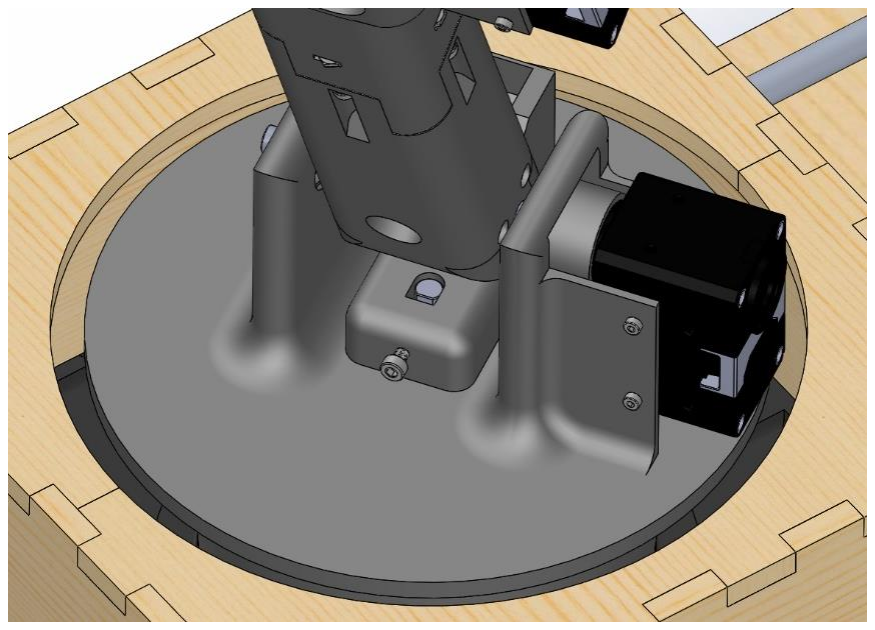
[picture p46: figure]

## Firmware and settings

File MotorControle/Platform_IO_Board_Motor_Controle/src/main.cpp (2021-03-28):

#ifndef UNIT_TEST

#include <Arduino.h>
#include <ArduinoJson.h>

#include "Comm/SerialComm.h"
#include "Comm/ControlMessage.h"
#include "Comm/MessageIO.h"
#include "DriveManager.h"
#include "StepperJoin.h"


//#define BAUD 9600 
#define BAUD 115200 

MessageIO IO;
SerialComm SC(&Serial);

void setup() {
  Serial.begin(BAUD);
  IO.addDevice(&SC);
}

void loop() {

  ControlMessage* msg = IO.readMessage(0);
  
  if(msg != 0)
  {
    ControlMessage responce(msg->getType()+1, msg->getPayLoadSize(), msg->getPayload());
    IO.sendMessage(0,responce);
    delete msg;
  }else
  {
    //auto responce = ControlMessage(-1);
    //IO.sendMessage(0,responce);
  }
  
  // put your main code here, to run repeatedly:
}

#endif

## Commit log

2021-01-25 add arduinoJson lib to repos
2021-02-02 fix serial not boot on arduino
    [main.cpp]
2021-02-03 clean code and fix unittest Compilation problem
    [main.cpp]
2021-02-11 add frame and accumulator to python side
    add accumulator and frame #remove this messages
2021-02-21 Set UI for individual joint (#27)
    + set up a basic UI to control every joint of the robot
2021-02-21 Add tcp/ip on python side (#28)
    * add frame and accumulator to python side
    * add EthernetComModule
    * add server methode
2021-02-24 Add Mechanical files and part (#30)
    * Add Mechanical files and part
    [1XTendeurPART1.STL, 1XTendeur_PART2.STL, 1X_Base_Controler.STL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]
2021-02-24 Update OpenCr Classes for Motor Control (#47)
    * Implementation of motors controls with the OpenCr card
    * Add limites fonctions
    * Add Home Position command
    * Update GoToHome function and Home position
    * Add ResetPosition command
    * Update OpenCr Classes for Motor Control
    * Deleate unused library
2021-02-24 Create joint classes and associated (#46)
    * Create join classes&cie
    * Compilations' test of OpenCR card
    * add Dynapixel2arduino Lib
    * Remove Dynamixel2Arduino library
    * Add motor test
    * Add DynamixelMotor code
    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
2021-03-28 Create stepper join for new steppermotor (#59)
    * Add_Stepper_28BYJ_48_library
    * create engine functions (goTo)
    * Add StepperJoin function
    * change the location of the library
    * Bug and fix after code review
    [main.cpp]
2021-03-30 Implement inverse kinematic (#60)
    * rename pathsolver into Cinematic
    * add a position solver based on gradient descent
    * add basic squelleton for the robot
2021-04-11 Fix arm ethernet compatibility (#65)
    * remove windows error tag and fix raspian bug
2021-04-11 add Gripper Rate Control (#71)
    * add Gripper Rate Control
2021-04-16 Final UI (#73)
    * Redesigned UI
    - Changed sliders to spin boxes
    - Added speed spin boxes
    - Added tab windows
    - Changed window layout
    - Changed text font
    - Added buttons for future features
    - Added tab for adding features for saving/loading files
    * Added cartesian and home features
    - Added input for cartesian coordinates;
    - Changed Speed section to Cartesian section;
    - Added set home and go to home features;
    - Changed spin boxes to double spin boxes;
    - Added buttons and plaintextedit for Save/Load tab
    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
2021-04-16 Create state manager (#75)
    * Add temporary main
    * Update StateManager
    * Clean the code
    * Update main and configure physical test for steppermotor
    * Code review Correction #1
    * Update main.cpp
    * Update main for physical test
    * Add StateManager class and test
    * Update Test for StateManager
    * Add Unitest for StepperJoin
    * Update Test_StateManager.cpp
    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
2021-04-16 Update OpenCr code
    * Add_StepperMotor_Class
    * Update main.ino
    * Update main.ino V2.3
    * Add Servo Motor
    * Add automatic initialisation
    * Final main.ino
2021-04-16 Create BOM.xls (#80)
    [BOM.xls]
2021-04-17 Deleate mec
    [1XTendeurPART1.STL, 1XTendeur_PART2.STL, 1X_Base_Controler.STL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]
2021-04-17 Create Assembly manual.pdf
2021-04-17 Add README MotorControle

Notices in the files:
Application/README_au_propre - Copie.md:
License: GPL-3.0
